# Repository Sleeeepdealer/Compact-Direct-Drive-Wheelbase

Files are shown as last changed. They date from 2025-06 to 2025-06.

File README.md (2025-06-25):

# Compact-Direct-Drive-Wheelbase
This project is an open-source, low-budget DIY force feedback wheelbase project designed as an affordable and accessible solution for sim-racing enthusiasts.

## The project uses:
- [FFBeast](https://ffbeast.github.io/docs/en/wheel.html) as the controller firmware.
- An ODrive Mini as the electronic speed controller.
- A hoverboard motor as the drive system.
- A magnetic encoder installed inside the motor: [MT6835 (10,000 PPR)](https://github.com/mcells/mt6835-hoverboard-motor?tab=readme-ov-file) or [MT6701 (1024 PPR)](https://www.printables.com/model/934160-ffbeast-encoder-assembly)
- A compact housing for the components - all design files included.

#

<p float="middle">
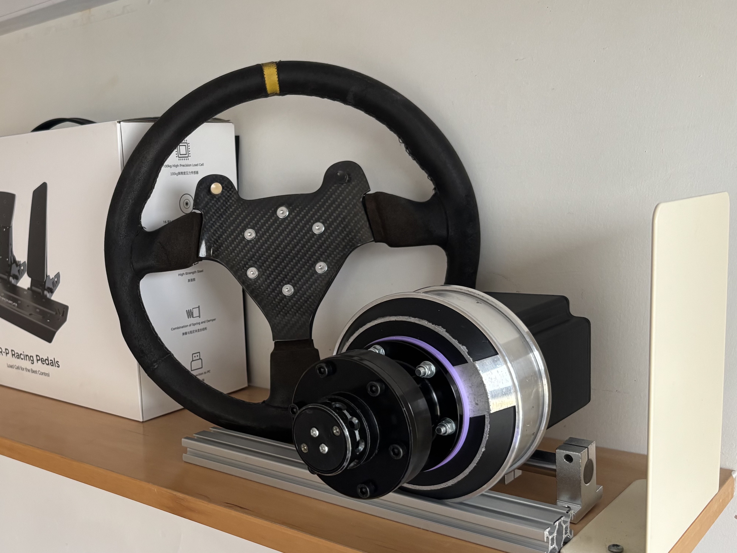
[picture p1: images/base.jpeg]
  
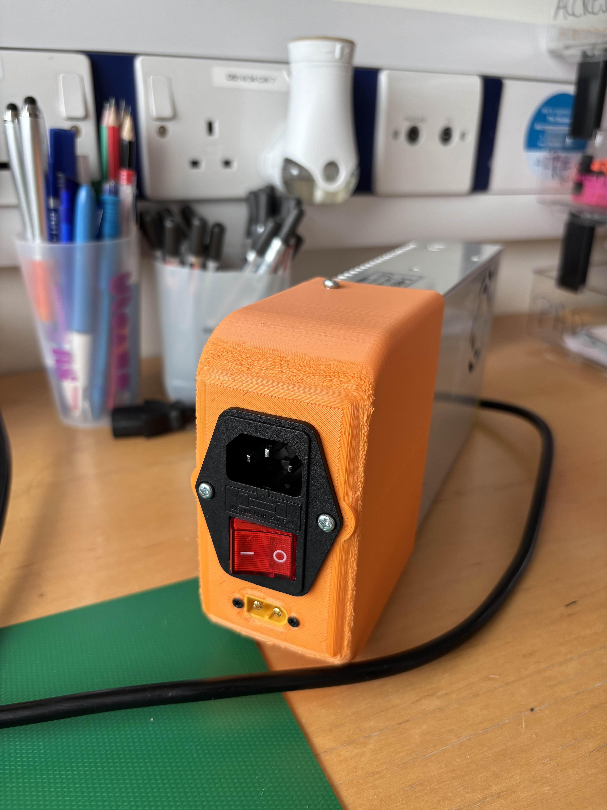
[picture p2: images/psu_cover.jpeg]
  
</p>

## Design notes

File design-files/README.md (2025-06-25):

## Design Files Notes

The STEP files use **colour-coded faces** to provide clear guidance for 3D printing and assembly.

---

## Colour Code Key

| Colour | Meaning |
| - | - |
| **Blue** | **Print orientation face** - this face should be placed flat on the print bed. |
| **Red** | **Heat insert location** - threaded heat inserts should be installed in this region. |

---

## Recommended 3D Print Settings

- Layer height: 0.2mm
- Infill density: 60%
- Wall line count: 4 (1.6mm)
- Top/bottom layers: 4 (0.8mm)
- Suppot: ON

---

## Heat Insert Guidance

- Press the threaded heat inserts into the parts with a ~220°C soldering iron (PLA). Please be patient when doing so and do NOT increase the temperature, as the parts may not be able to hold the threaded heat inserts if melted too much.
- Once the inserts are flush with the surrounding surface, remove the soldering iron and gently press down with a flat object (I used a metal ruler) to ensure it stays fully seated as the surrounding plastic solidifies.

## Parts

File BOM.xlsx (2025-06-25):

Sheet: Fasteners
Part Name | Quantity | Link | Notes
M3xD4.2XL4.0 brass inserts | 20 | https://www.aliexpress.com/item/1005007342105110.html | You need 4 for the front, 14 for the body, and 2 for the PSU cover
M3x10 pan head screws | 18 | https://www.aliexpress.com/item/1005004531602992.html | You need 18 of these for the front, body, and rear
M3x10 countersunk screws | 2 | https://www.aliexpress.com/item/1005004533251852.html | You need 2 for the PSU cover
M3x6 self-tapping pan head screws | 3 | https://www.aliexpress.com/item/1005007342873516.html | You need 3 for the encoder mount
M4x6 pan head screws | 3 | https://www.aliexpress.com/item/1005004531602992.html | You need 3 for the PSU cover
M5x25 pan head screws | 10 | https://www.aliexpress.com/item/1005004531602992.html | You need 4 for the wheelbase and 6 for the hub extension
M5 nyloc nuts | 10 | https://www.aliexpress.com/item/1005004649590892.html | You need 4 for the wheelbase and 6 for the hub extension
M3 flat washers | 18 | https://www.aliexpress.com/item/1005004708825326.html | You need to use these under all bolts and nuts
M4 flat washers | 3 | https://www.aliexpress.com/item/1005004708825326.html | You need to use these under all bolts and nuts
M5 flat washers | 20 | https://www.aliexpress.com/item/1005004708825326.html | You need to use these under all bolts and nuts

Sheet: Electronics
Part Name | Quantity | Link | Notes
Hoverboard motor | 1
FFBeast reference PCB | 1 | https://oshwlab.com/olukelo/ffb-breakout | This is NOT optional, as the case will be mounted onto this PCB.
ODrive / XDrive mini | 1 | https://www.aliexpress.com/item/1005008155597487.html | This comes with 2x JST-GH 1.25 cables for the encoder and GPIO pins and 1x 50W 2J braking resistor. You do NOT need to purchase these again.
Encoder (MT6701) | 1 | https://www.aliexpress.com/item/1005008109162273.html | I recommend getting two if it's your first time soldering, as it's not uncommon for people to mess up this part. This comes with 1x diameter magnet. You do NOT need to purchase it again.
24V 20A PSU | 1 | https://www.aliexpress.com/item/1005006332585327.html | You can use any 24V 20A supply, but only the linked one will work with the PSU cover included in the files.

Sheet: Connectors
Part Name | Quantity | Link | Notes
XT60PW-M | 1 | https://www.aliexpress.com/i/1005008002139843.html | For reference PCB
USB-B10-BRW | 1 | https://www.aliexpress.com/item/1005008808984785.html | For reference PCB
XT60E-M | 1 | https://www.aliexpress.com/item/1005007657086234.html | For PSU out
XT60H-F | 2 | https://www.aliexpress.com/item/1005007119012780.html | For connecting PSU out to reference PCB in
MR30-F | 1 | https://www.aliexpress.com/item/1005008880234116.html | For connecting motor to controller
MR30-M | 1 | https://www.aliexpress.com/item/1005008880234116.html | For connecting motor to controller
AM1015E-F | 1 | https://www.aliexpress.com/item/1005008576809245.html | For connecting braking resistor to controller
AM1015E-M | 1 | https://www.aliexpress.com/item/1005008576809245.html | For connecting braking resistor to controller
4-pin USBC-M (Optional) | 1 | https://www.aliexpress.com/item/1005006524724636.html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: | For connecting the controller to the reference PCB
C14 socket | 1 | https://www.aliexpress.com/item/4001089659222.html | For connecting the outlet to PSU. I recommend getting the plug with cables included, this will save you alot of work (and money) crimping the leads yourself and keep you safe.
C13 cable | 1 | https://www.aliexpress.com/item/1005007044430647.html | For connecting the outlet to PSU. Any C13 cable will work. The outlet-end depends on where you live.

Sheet: Mounting
Part Name | Quantity | Link
SK16 | 6 | https://www.aliexpress.com/item/32775746125.html
16mm shaft | 1 | https://www.aliexpress.com/item/32332798910.html
51mm hub extender | 1 | https://www.aliexpress.com/item/32883662045.html | Any hub extender with a 70mm bolt pattern will work. That said, it will be more difficult to install the encoder if you are to use a longer hub extender.
Quick release | 1 | https://www.aliexpress.com/item/1005006220085591.html | This comes with 12x M5 screws required to attach both the wheel-side and base-side QR. You do NOT need to purchase these again.

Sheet: Prints
Part Name | Quantity | Link | Notes
Front | 1 |  | Recommended material: PLA. You can get these printed yourself, via a local service, or outsource it to a manufacturer of your choice.
Body | 1 |  | Recommended material: PLA. You can get these printed yourself, via a local service, or outsource it to a manufacturer of your choice.
Rear | 1 |  | Recommended material: PLA. You can get these printed yourself, via a local service, or outsource it to a manufacturer of your choice.
PSU Cover | 1 |  | Recommended material: PLA. You can get these printed yourself, via a local service, or outsource it to a manufacturer of your choice.
Encoder support piece | 1 | https://www.printables.com/model/934160-ffbeast-encoder-assembly/files | Recommended material: PETG. You can get these printed yourself, via a local service, or outsource it to a manufacturer of your choice.
Centering piece | 1 | https://www.printables.com/model/934160-ffbeast-encoder-assembly/files | Recommended material: PETG. You can get these printed yourself, via a local service, or outsource it to a manufacturer of your choice.
Magnet carrier piece | 1 | https://www.printables.com/model/934160-ffbeast-encoder-assembly/files | Recommended material: PETG. You can get these printed yourself, via a local service, or outsource it to a manufacturer of your choice.

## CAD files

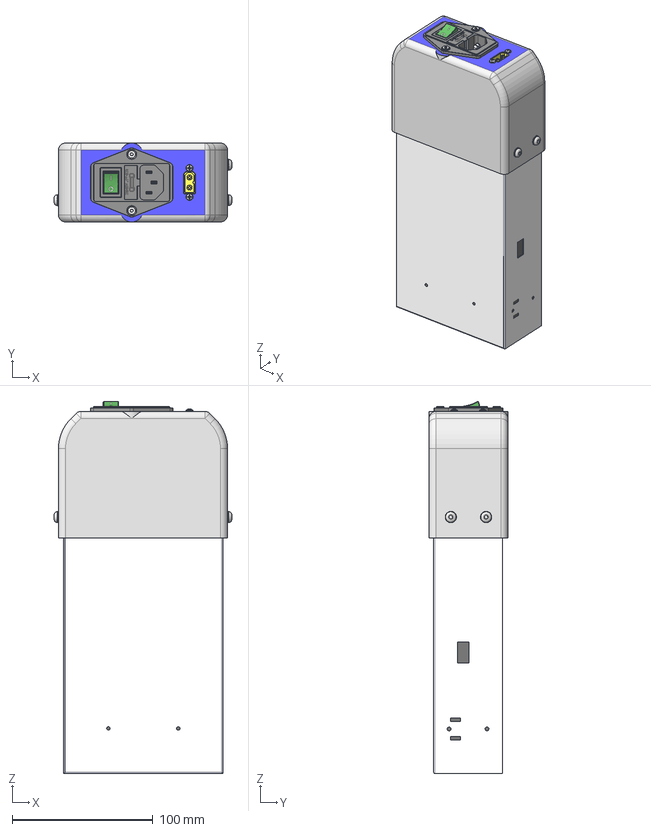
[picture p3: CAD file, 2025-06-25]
design-files/reference-assembly/PSU_assy.stp
126.0 x 56.0 x 263.9 mm
AS 1427 - M2.5 x 8 x 2
AS 1237 - 4 x 5
ANSI B18.2.4.2M - M4x0.7 x 2
ANSI B18.3.4M - M4 x 0.7 x 4, BHSBHCSM x 3
ASME/ANSI B18.3.5M - M3x10(2) x 2
AS 1112 - M2.5 Type 5 x 2
PSU cover
XT60E-M
C14
PSU_1

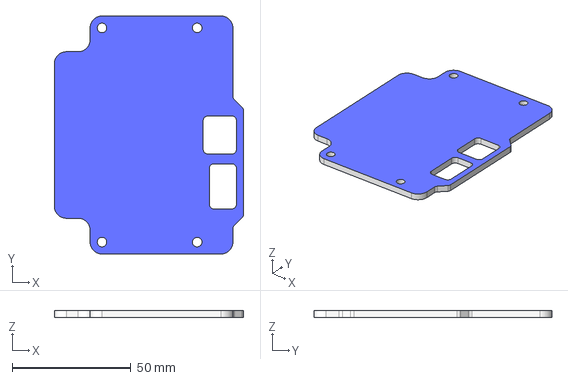
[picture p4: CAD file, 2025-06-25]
design-files/Rear.stp
79.5 x 100.0 x 3.00 mm

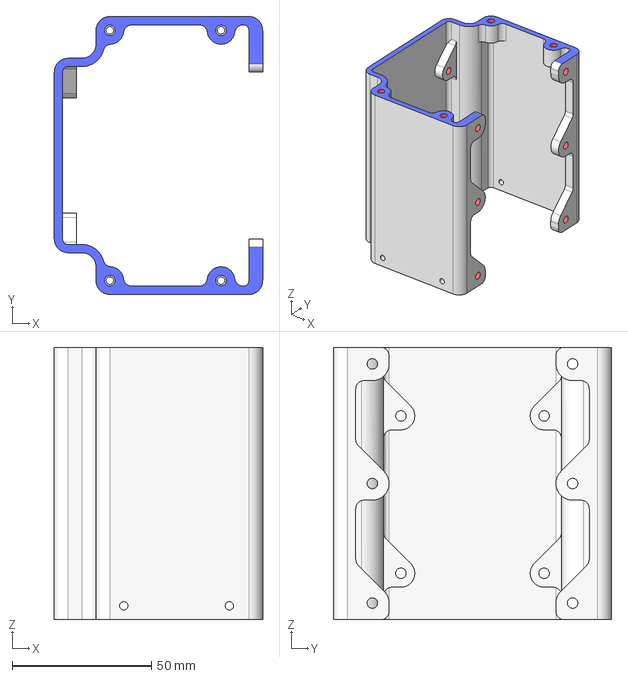
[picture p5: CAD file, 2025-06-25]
design-files/Body.stp
75.0 x 100.0 x 98.0 mm

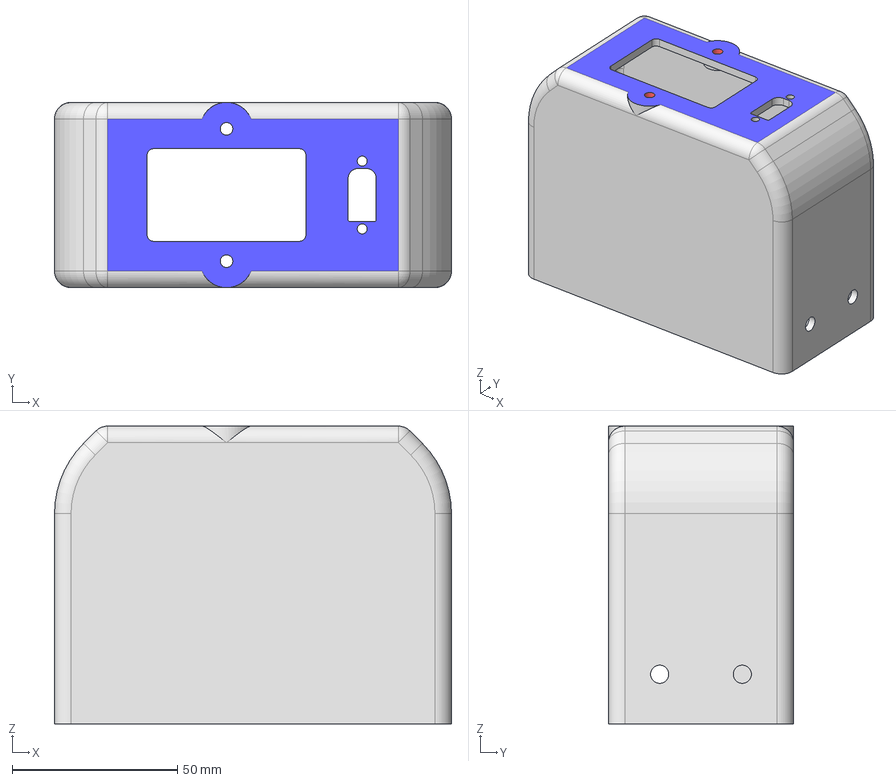
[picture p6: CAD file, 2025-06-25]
design-files/PSU_cover.stp
120.0 x 56.0 x 90.0 mm

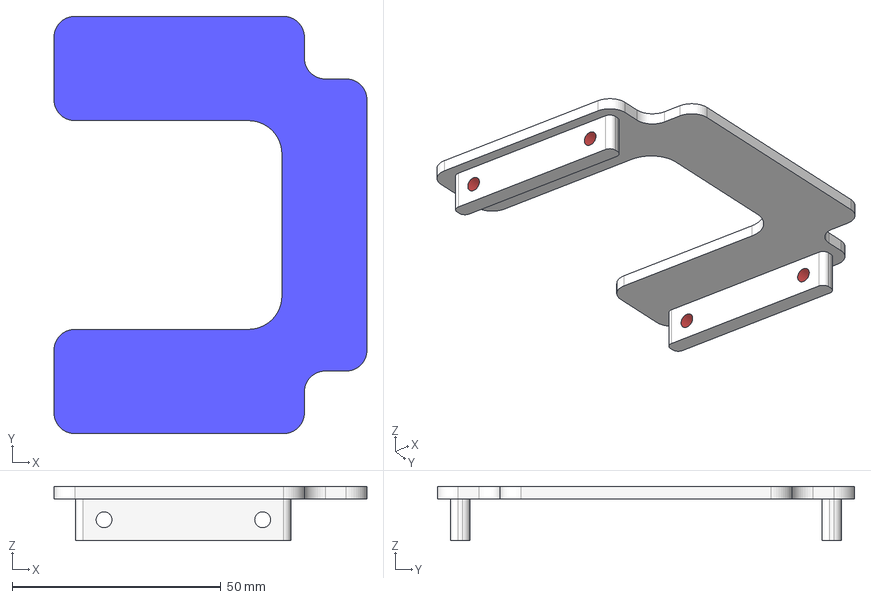
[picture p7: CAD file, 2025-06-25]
design-files/Front.stp
75.0 x 100.0 x 13.0 mm
